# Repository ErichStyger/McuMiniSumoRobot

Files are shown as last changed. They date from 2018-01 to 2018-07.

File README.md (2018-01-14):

# McuMiniSumoRobot
This project implements the hardare and software for a Mini Sumo Robot.
The project has been started and created by Simon Herzog as part of the PAIND course at the Lucerne University of Applied Sciences and Arts in the Fall 2017 semester.

This small (10x10 cm) competitive, cost effective Mini Sumo robot is itended to be used for
- robotics courses
- computer science courses
- electrical engineering courses
- MINT and STEM activites
- show case for conferences and exhibitions 
- fun projects

See https://github.com/ErichStyger/McuMiniSumoRobot/wiki for more details about this project.

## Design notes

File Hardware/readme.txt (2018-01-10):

This folder contains the hardware/PCB files and information (KiCAD).
The V1 folder contains the first version of the PCB.

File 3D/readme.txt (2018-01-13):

This folder contains 3D models for 3D printing.
Autodesk 123D Design has been used to create the .123dx files.

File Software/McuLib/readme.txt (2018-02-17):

readme.txt
----------
This folder McuLib contains files from the McuOnEclipse library:
https://github.com/ErichStyger/McuOnEclipseLib

This folder contains all the library sources:
- config: application specific configuration files
- src: source files

Middleware:
- FreeRTOS: FreeRTOS realtime operating system, optimized and tuned for Segger SystemView and Percepio Trace
- TraceRecorder: Percipio Tracealyzer library for FreeRTOS (https://percepio.com/tz/)
- SEGGER_RTT: Segger Realtime Terminal Library (https://www.segger.com/products/debug-probes/j-link/technology/real-time-transfer/about-real-time-transfer/)
- SEGGER_SysView: Segger Systemview Library for tracing FreeRTOS (https://www.segger.com/products/development-tools/systemview/)

Components of the McuOnEclipse (in alphabetical order):
- McuArmTools: various ARM Cortex utilities
- McuCriticalSection: critical section handling
- McuDS18B20: Driver for the DS18B20 One-Wire temperature sensor library
- McuEvents: event handling using a bit array
- McuFontDisplay: Font rendering for graphical displays
- McuFXOS8700: Driver for the NXP FXOS8700 accelerometer/magnetometer
- McuGDisplay: Driver for graphical displays
- McuGenericI2C: Generic I2C driver using hardware I2C or software I2C
- McuGenericSWI2C: Software (bit banging) I2C driver
- McuGenericSWSPI: Software (bit banging) SPI driver
- McuGFont: Graphical font library driver. Several fonts are available in the 'fonts' subfolder
- McuHardfault: ARM Cortex-M hardfault handler
- McuI2CSpy: I2C sniffing utility
- McuLED: generic LED driver
- McuLib: Configuration of the McuOnEclipse Library
- McuOneWire: 1-Wire communication driver
- McuPercepio: Configuration and interface to the Percepio Trace library
- McuPidFloat: Generic PID control loop using floating point values
- McuPidInt: Generic PID control loop using integer values
- McuQuadCounter: Quadrature Counter library
- McuRingBuffer: Generic Ring Buffer implementation
- McuRTOS: wrapper for FreeRTOS
- McuRTT: wrapper for Segger RTT
- McuSharpMemoryDisplay: Driver for the Sharp Memory displays
- McuShell: Driver for a command line shell
- McuSystemView: Wrapper for the Segger SystemViewer
- McuTimeDate: Realtime clock implementation for software, hardware and external I2C RTC
- McuTimeout: generic driver for timeout handling
- McuTrigger: generic interrupt callback handling
- McuUSB: interface and wrapper to the FSL USB Stack 4.1.1
- McuUtility: various safe string manipulation and other utility functions
- McuWait: Realtime synchronization waiting routines
- McuXFormat: tiny formatting and printing, similar to sprintf

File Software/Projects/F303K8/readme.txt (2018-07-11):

readme.txt
----------

Project for the Sumo robot using the STM32F303 Nucleo-3 board.

Open:
- display more robot status on LCD
- line following
- UART
- option: haptic feedback with wheels
- Use UART for one extra line sensor and to turn off IR LEDs
- header for LCD, pull-ups

Custom configuration settings (McuLib/config):
- McuShellconfig.h
- McuSSD1306config.h
- McuGenericI2Cconfig.h

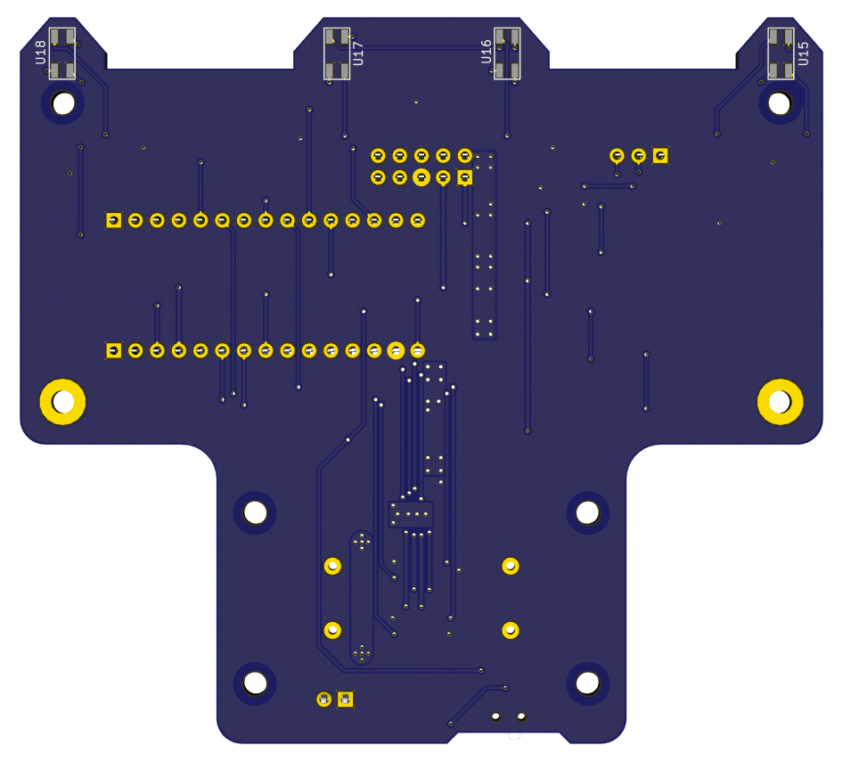
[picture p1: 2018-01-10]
Hardware/V1a/3D_PCB_bottom.png

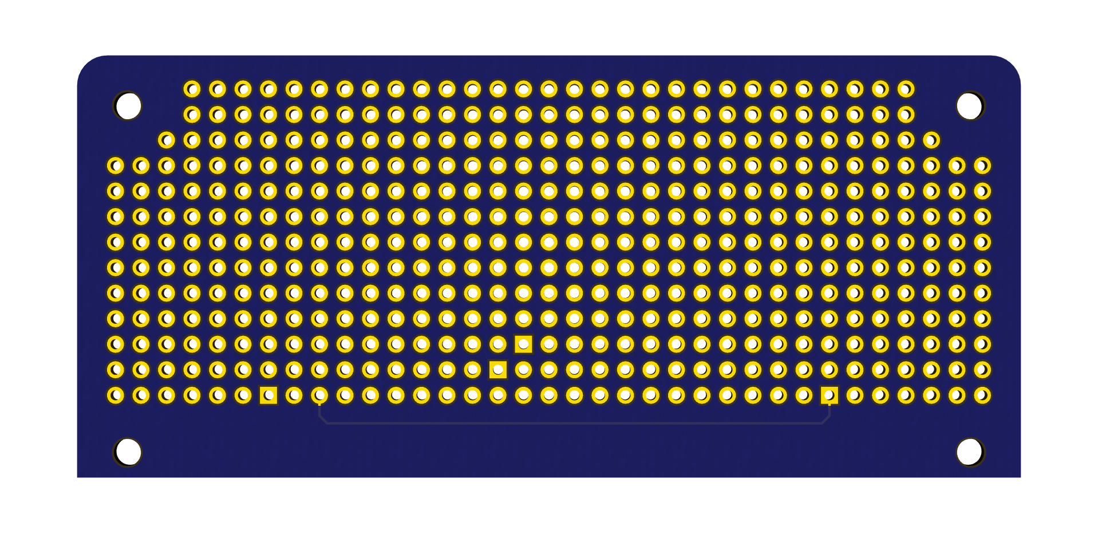
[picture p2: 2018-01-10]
Hardware/V1a/3D_PCB_top_back.png

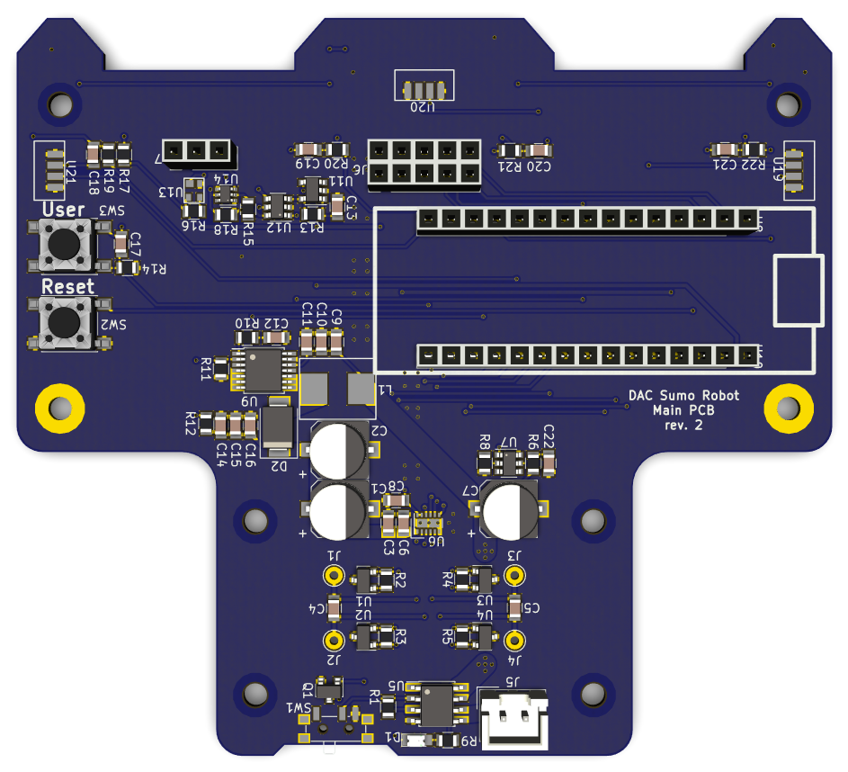
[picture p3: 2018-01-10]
Hardware/V1a/3D_PCB_top.png

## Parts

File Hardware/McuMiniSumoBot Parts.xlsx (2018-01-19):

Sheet: Summary
Cost estimate for a single Robot
 | Total | CHF 112.50 |  |  |  | CHF 96.40 | CHF 17.23
Vendor | Order Number | Shipping | Min | Add | Price | Total |  | Description | Comment | Link
Mouser | 710-15400394A3590 |  | 6 |  | 0.42 | 2.53 | 0.00 | Standard LEDs - Through Hole WL-TIRW THT Infrared Waterclr Rnd 5mm 940 nm |  | https://www.mouser.ch/productdetail/wurth-electronics/15400394a3590
Mouser | Various |  | 1 |  | 27.11 | 27.11 | 0.00 | PCB Parts, see other Tab | See other tab with details
Mouser | 511-NUCLEO-F303K8 |  | 1 |  | 10.50 | 10.50 | 0.00 | Nucleo |  | https://www.mouser.ch/ProductDetail/STMicroelectronics/NUCLEO-F303K8/
Banggood | 969144 |  | 0 | 1 | 6.18 | 0.00 | 6.18 | 0.96 Inch 4Pin Blue Yellow IIC I2C OLED Display Module For Arduino | Order pack of 3 | https://www.banggood.com/0_96-Inch-4Pin-Blue-Yellow-IIC-I2C-OLED-Display-Module-For-Arduino-p-969144.html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
Banggood | 969147 |  |  | 1 | 6.28 |  |  | 0.96 Inch 4Pin IIC I2C Blue OLED Display Module For Arduino |  | https://www.banggood.com/0_96-Inch-4Pin-IIC-I2C-Blue-OLED-Display-Module-For-Arduino-p-969147.html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
Banggood | 924048 |  | 1 |  | 1.53 | 1.53 | 0.00 | USB Lithium Battery Charger Module Board With Charging And Protection | Oder pack of 3 | https://www.banggood.com/USB-Lithium-Battery-Charger-Module-Board-With-Charging-And-Protection-p-924048.html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
Banggood | 1091243 |  | 1 | 4 | 2.76 | 2.76 | 11.05 | 5Pcs XF Power 3.7V 600mAh 1S 30C Fabric Cable LiPo Battery White Plug | Order pack of 5 | https://www.banggood.com/XF-Power-3_7V-600mAh-1S-30C-Fabric-Cable-LiPo-Battery-White-Plug-p-1091243.html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
Banggood | 1044078 |  | 1 |  | 2.52 | 2.52 | 0.00 | 10 Pairs 1S Battery Charging Cable Male & Female | Use correct connector instead
Banggood | Shipping |  |  |  |  | 0.00 | 0.00 |  | Usually free of charge shipping | https://www.pcbway.com/
PCBWay | Shipping | CHF 11.00 |  |  |  | 0.00 | 0.00
PCBWay | PCB |  | 1 |  | 5.00 | 5.00 | 0.00 | PCB 10x10 dual layer | 5-10 PCBs for a total of $5!
Jsumo | SLT20 |  | 1 |  | 16.00 | 16.00 | 0.00 | SLT20 Silicon Wheel Set
Jsumo | SLT20P |  |  |  | 18.00 | 0.00 | 0.00 | SLT20 Silicon Wheel Set with steel hub | Recommended
Jsumo | Shipping | CHF 40.00 |  |  |  | 0.00 | 0.00 |  | Free shipping from $199
Fingertech |  |  |  |  |  | 0.00 | 0.00 |  | Alternative wheels, don't forget Hex Wrench!
Pololu | 1127 |  |  |  | 3.56 | 0.00 | 0.00 | 1: Solarbotics RW2i Wheel (internal set screw) | Alternative wheels, don't forget Hex Wrench! | https://www.pololu.com/product/1127
Pololu | 2214 |  |  |  | 16.95 | 0.00 | 0.00 | 2: 100:1 Micro Metal Gearmotor HP 6V with Extended Motor Shaft | 1:75, 1:100 and 1:150 alternatives | https://www.pololu.com/product/2214
Pololu | 2599 |  | 1 |  | 3.45 | 3.45 | 0.00 | Magnetic Encoder Disc for Micro Metal Gearmotors, OD 7.65 mm, ID 1.0 mm, 12 CPR (Bulk) | Bulk 5 pieces
Pololu | Shipping | CHF 40.00 |  |  |  | 0.00 | 0.00
Mouser | Shipping | CHF 8.00 |  |  |  | 0.00 | 0.00 |  | Free shipping inside US
TinySine | Shipping | CHF 6.00 |  |  |  | 0.00 | 0.00
TinySine | G5A1518B927942 | CHF 7.50 | 2 |  | 7.50 | 15.00 | 0.00 | Micro Metal Gearmotor HP 6V with Extended Motor Shaft 1.6A - 100:1 |  | https://www.tinyosshop.com/index.php?route=product/product&path=64_82&product_id=1051
Misc | Misc small parts |  | 1 |  | 10.00 | 10.00 | 0.00

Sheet: PCB Parts
DAC SUMO ROBOT |  |  |  |  |  |  |  |  | 27.11
Mouser-Nr. | Herst.- Nr. | Hersteller | Kunden-Teilenr | Beschreibung | RoHS | Lebenszyklus | Stückzahl | Preis (CHF) | Gesamtpreis: (CHF)
80-EDH227M010A9HAA | EDH227M010A9HAA | KEMET |  | Alu-Elektrolytkondensatoren - SMD 10V 220uF 20% | RoHS-konform | Neues Produkt | 3 | 0.343 fr. | 1.03
511-STTH4R02U | STTH4R02U | STMicroelectronics |  | Gleichrichter RECTIFIER | RoHS-konform |  | 1 | 0.782 fr. | 0.78
771-NX7002AKVL | NX7002AKVL | Nexperia |  | MOSFET NX7002AK/TO-236AB/REEL 11" Q3/ | RoHS-konform |  | 1 | 0.117 fr. | 0.12
688-SSSS811101 | SSSS811101 | ALPS |  | Schiebeschalter SPDT HORZ GRND 1.5mm | RoHS-konform |  | 1 | 1.21 fr. | 1.21
926-LM2700MTXADJNOPB | LM2700MTX-ADJ/NOPB | Texas Instruments |  | Schaltspannungsregler 600kHz/1.25MHz, 2.5A, Step-up PWM DC/DC | RoHS-konform |  | 1 | 3.61 fr. | 3.61
595-DRV8835DSSR | DRV8835DSSR | Texas Instruments |  | Motor / Bewegung / Zündungscontroller und Treiber 1.5A Low Vlt Stepper Motor | RoHS-konform |  | 1 | 1.81 fr. | 1.81
78-TSSP77038TR | TSSP77038TR | Vishay |  | Infrarot-Receiver IR Receiver Module | RoHS-konform |  | 3 | 1.75 fr. | 5.25
595-DRV5013ADQDBZR | DRV5013ADQDBZR | Texas Instruments |  | Halleffekt-/Magnetsensoren für Plattenmontage 2.5-38V Dig Latch Hall Sensor | RoHS-konform |  | 4 | 0.831 fr. | 3.32
595-SN74LVC1G18DBVR | SN74LVC1G18DBVR | Texas Instruments |  | Encoder, Decoder, Multiplexer u. Demultiplexer 1 of 2 Noninverting DeMultxr | RoHS-konform |  | 1 | 0.362 fr. | 0.36
998-MIC1557YM5TR | MIC1557YM5-TR | Microchip |  | Zeitgeber & Support-Produkte | RoHS-konform |  | 1 | 0.929 fr. | 0.93
512-QRE1113GR | QRE1113GR | ON Semiconductor |  | Optische Schalter, reflektierend, mit Fototransistor-Ausgang Reflective Sensor | RoHS-konform |  | 4 | 0.841 fr. | 3.36
757-SSM6N7002KFULF | SSM6N7002KFU,LF | Toshiba |  | MOSFET Small-signal MOSFET 2in1 ESD Protected | RoHS-konform | Neues Produkt | 1 | 0.254 fr. | 0.25
653-B3FS-1010 | B3FS-1010 | Omron |  | Sensorschalter 6x6x4.3mm 100gf | RoHS-konform |  | 2 | 0.684 fr. | 1.37
512-FDS4935BZ | FDS4935BZ | ON Semiconductor |  | MOSFET 30V PCH DUAL POWER TRENCH M | RoHS-konform |  | 1 | 0.91 fr. | 0.91
621-AP9101CAK6ABTRG1 | AP9101CAK6-ABTRG1 | Diodes Incorporated |  | Batterie-Management Protection IC 1-Cell LI 3.0uA 3.5V | RoHS-konform |  | 1 | 0.43 fr. | 0.43
963-LMK212BBJ226MG-T | LMK212BBJ226MG-T | Taiyo Yuden |  | Kondensator aus mehreren Keramikschichten MLCC - SMD/SMT 22uF 10V X5R +/-20% 0805 Gen Purp | RoHS-konform |  | 2 | 0.311 fr. | 0.62
726-BCR205WH6327 | BCR 205W H6327 | Infineon |  | LED-Beleuchtungstreiber Ultra lowdropout LED controllr up to 80mA | RoHS-konform |  | 1 | 0.44 fr. | 0.44
710-150080VS75000 | 150080VS75000 | Wurth Electronics |  | Standard-LEDs - SMD WL-SMCW SMDMono TpVw Waterclr 0805 BrtGrn | RoHS-konform |  | 1 | 0.184 fr. | 0.18
652-SRP7028A-4R7M | SRP7028A-4R7M | Bourns |  | Festinduktoren 4.7uH 20% SMD 7028 AEC-Q200 | RoHS-konform |  | 1 | 1.13 fr. | 1.13

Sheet: NOT included
0805 R and C
Shipping (might vary)
Battery connector
Screws
Standoffs
3D Prints
PCB Assembly
Robot assembly
Headers (optional)

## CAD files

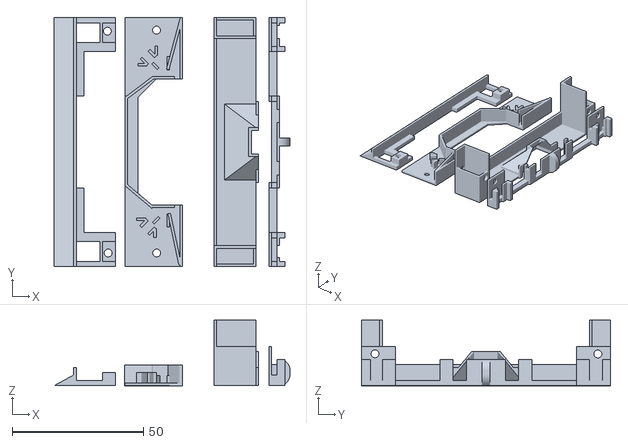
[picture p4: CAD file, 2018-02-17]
3D/FrontBlade.stl
90.0 x 95.1 x 25.1

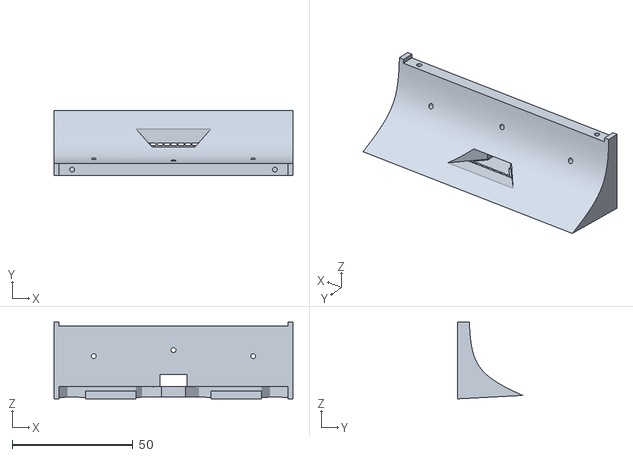
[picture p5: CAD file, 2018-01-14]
3D/Blade - Blade.stl
99.0 x 27.0 x 31.8

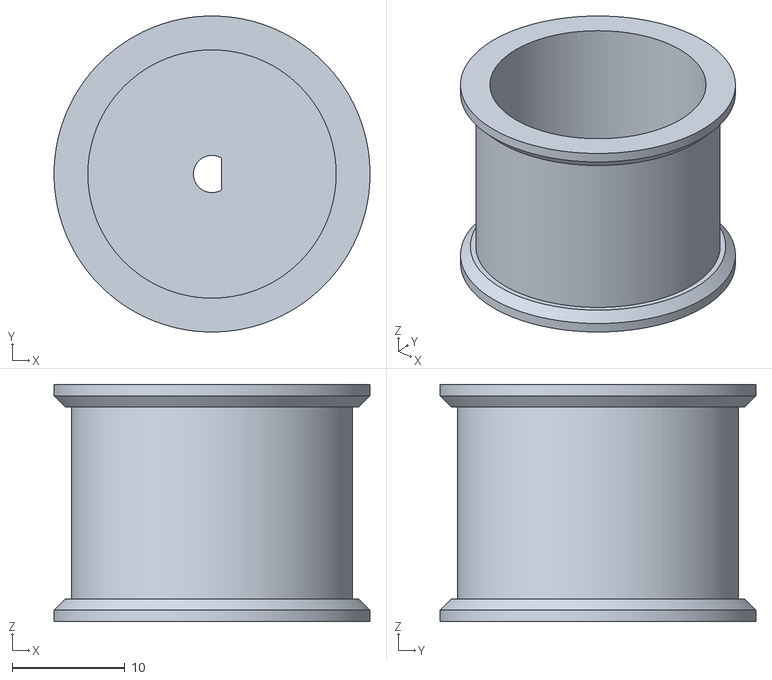
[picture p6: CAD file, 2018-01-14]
3D/Hub JSumo.stl
28.0 x 28.0 x 21.0

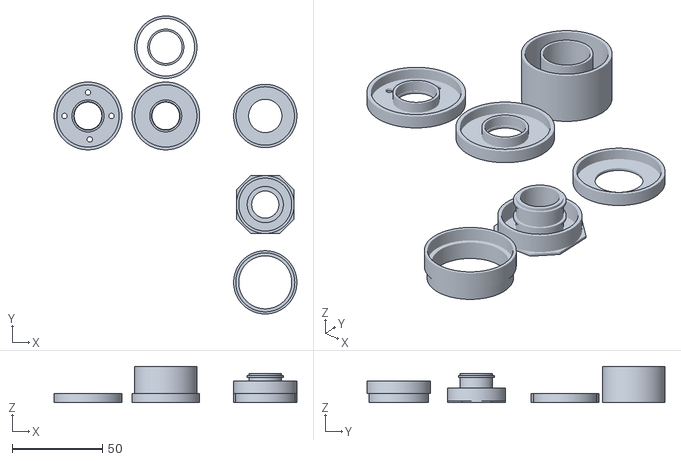
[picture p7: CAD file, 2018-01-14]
3D/TireMold.stl
134.2 x 164.7 x 20.0

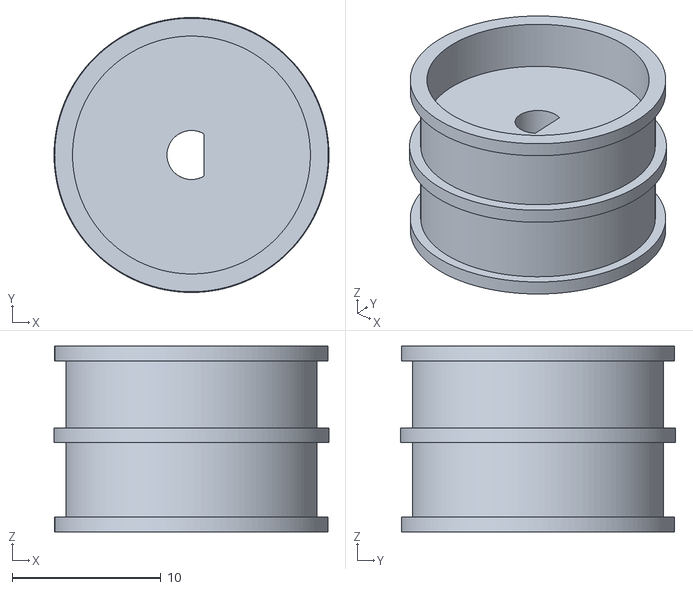
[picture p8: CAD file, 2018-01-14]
3D/Hub Solarbotics.stl
18.5 x 18.5 x 12.5

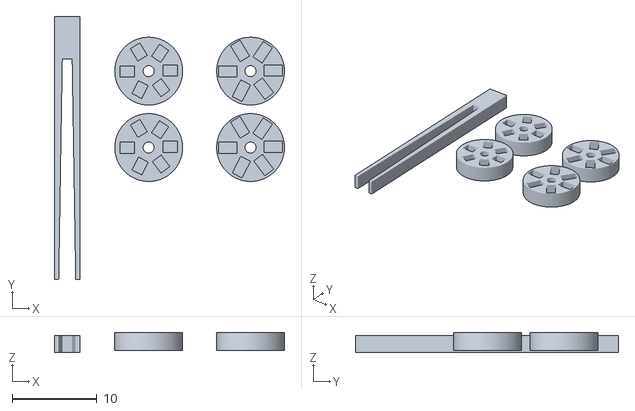
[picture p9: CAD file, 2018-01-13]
3D/MagneticDiskEncoder.stl
27.1 x 31.0 x 2.40

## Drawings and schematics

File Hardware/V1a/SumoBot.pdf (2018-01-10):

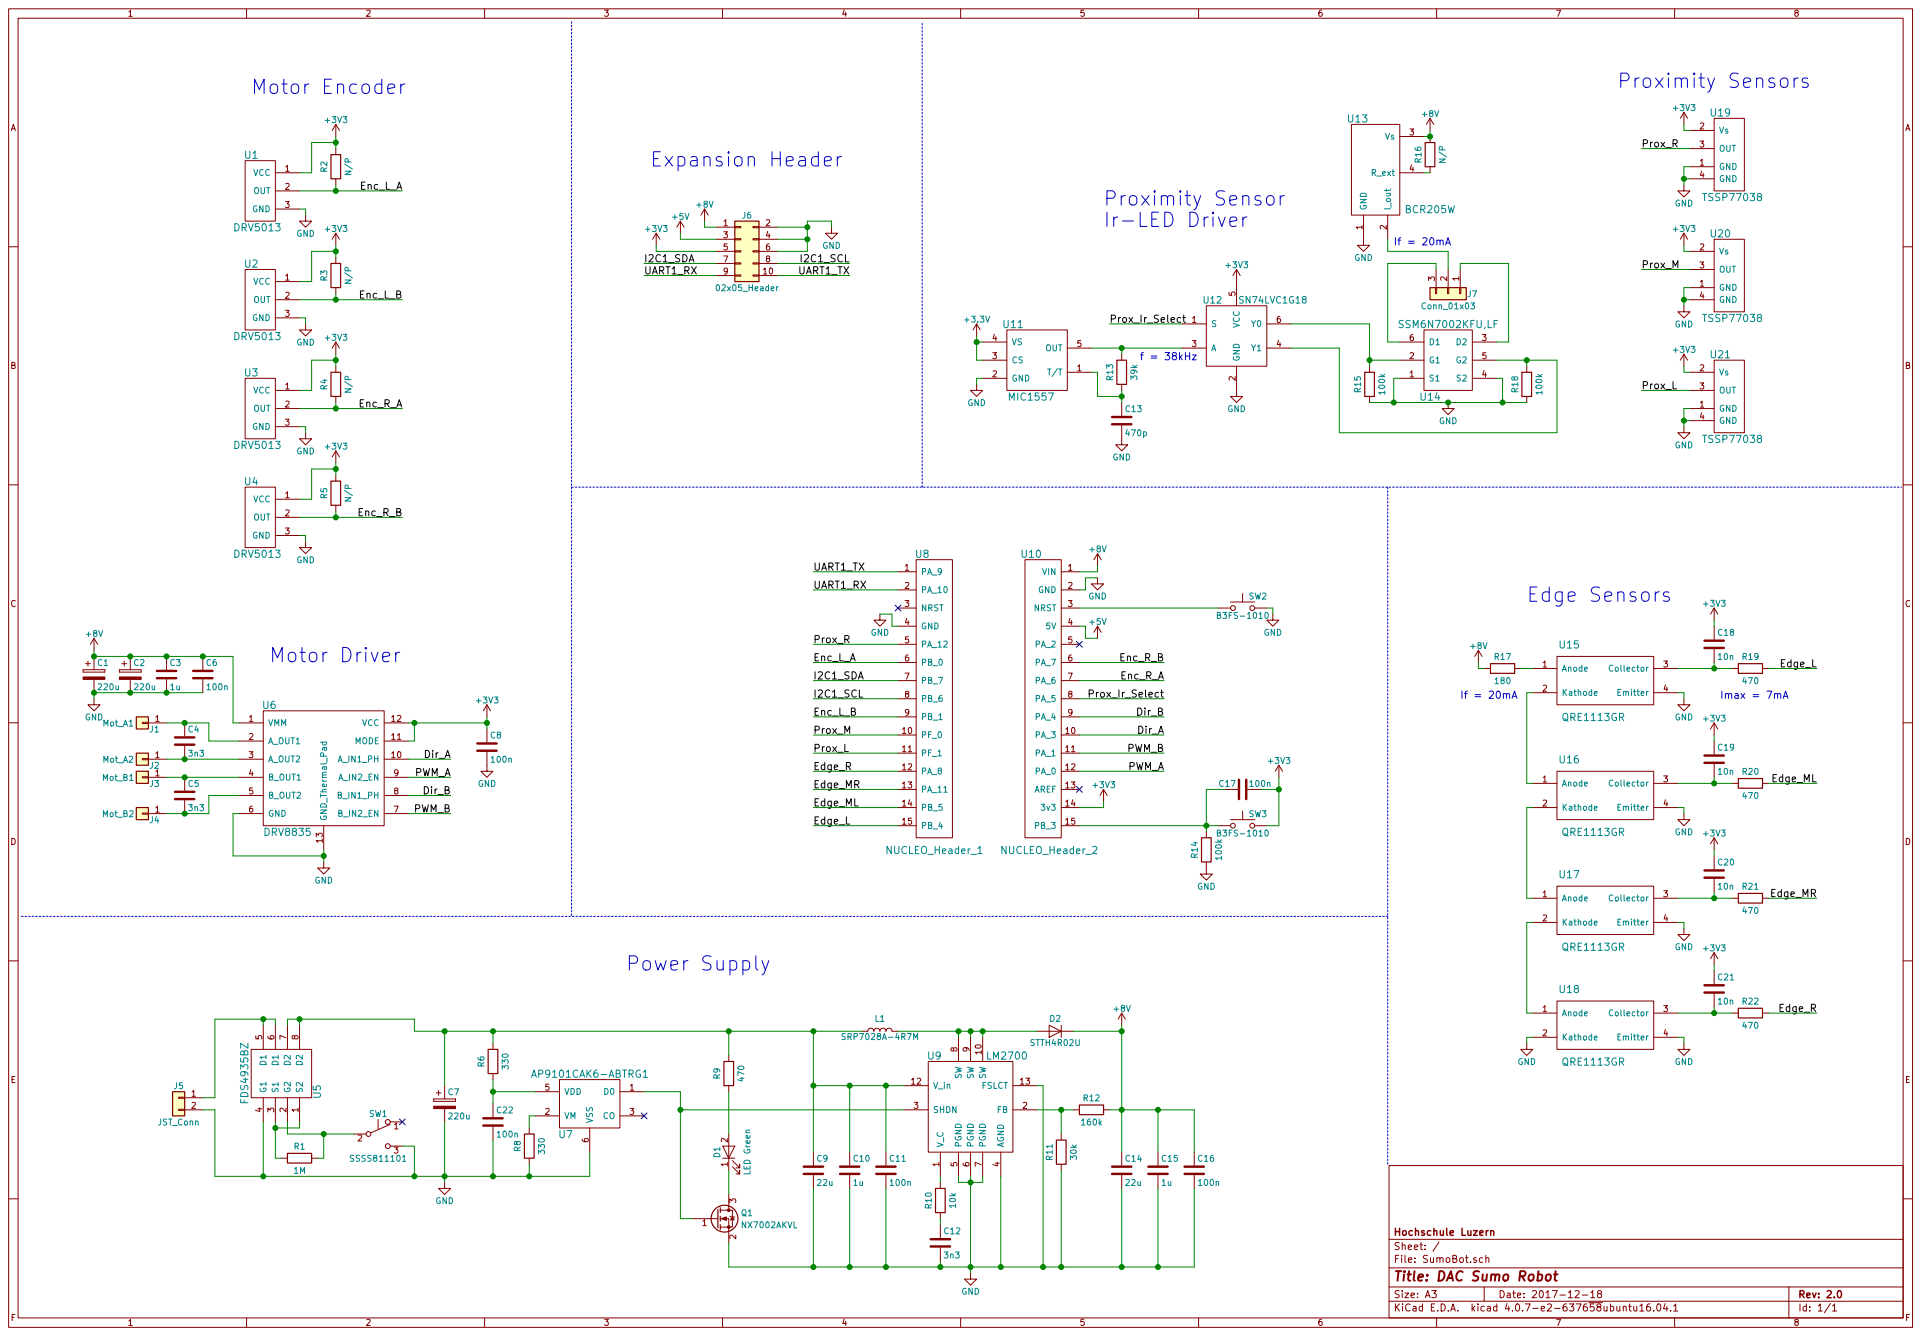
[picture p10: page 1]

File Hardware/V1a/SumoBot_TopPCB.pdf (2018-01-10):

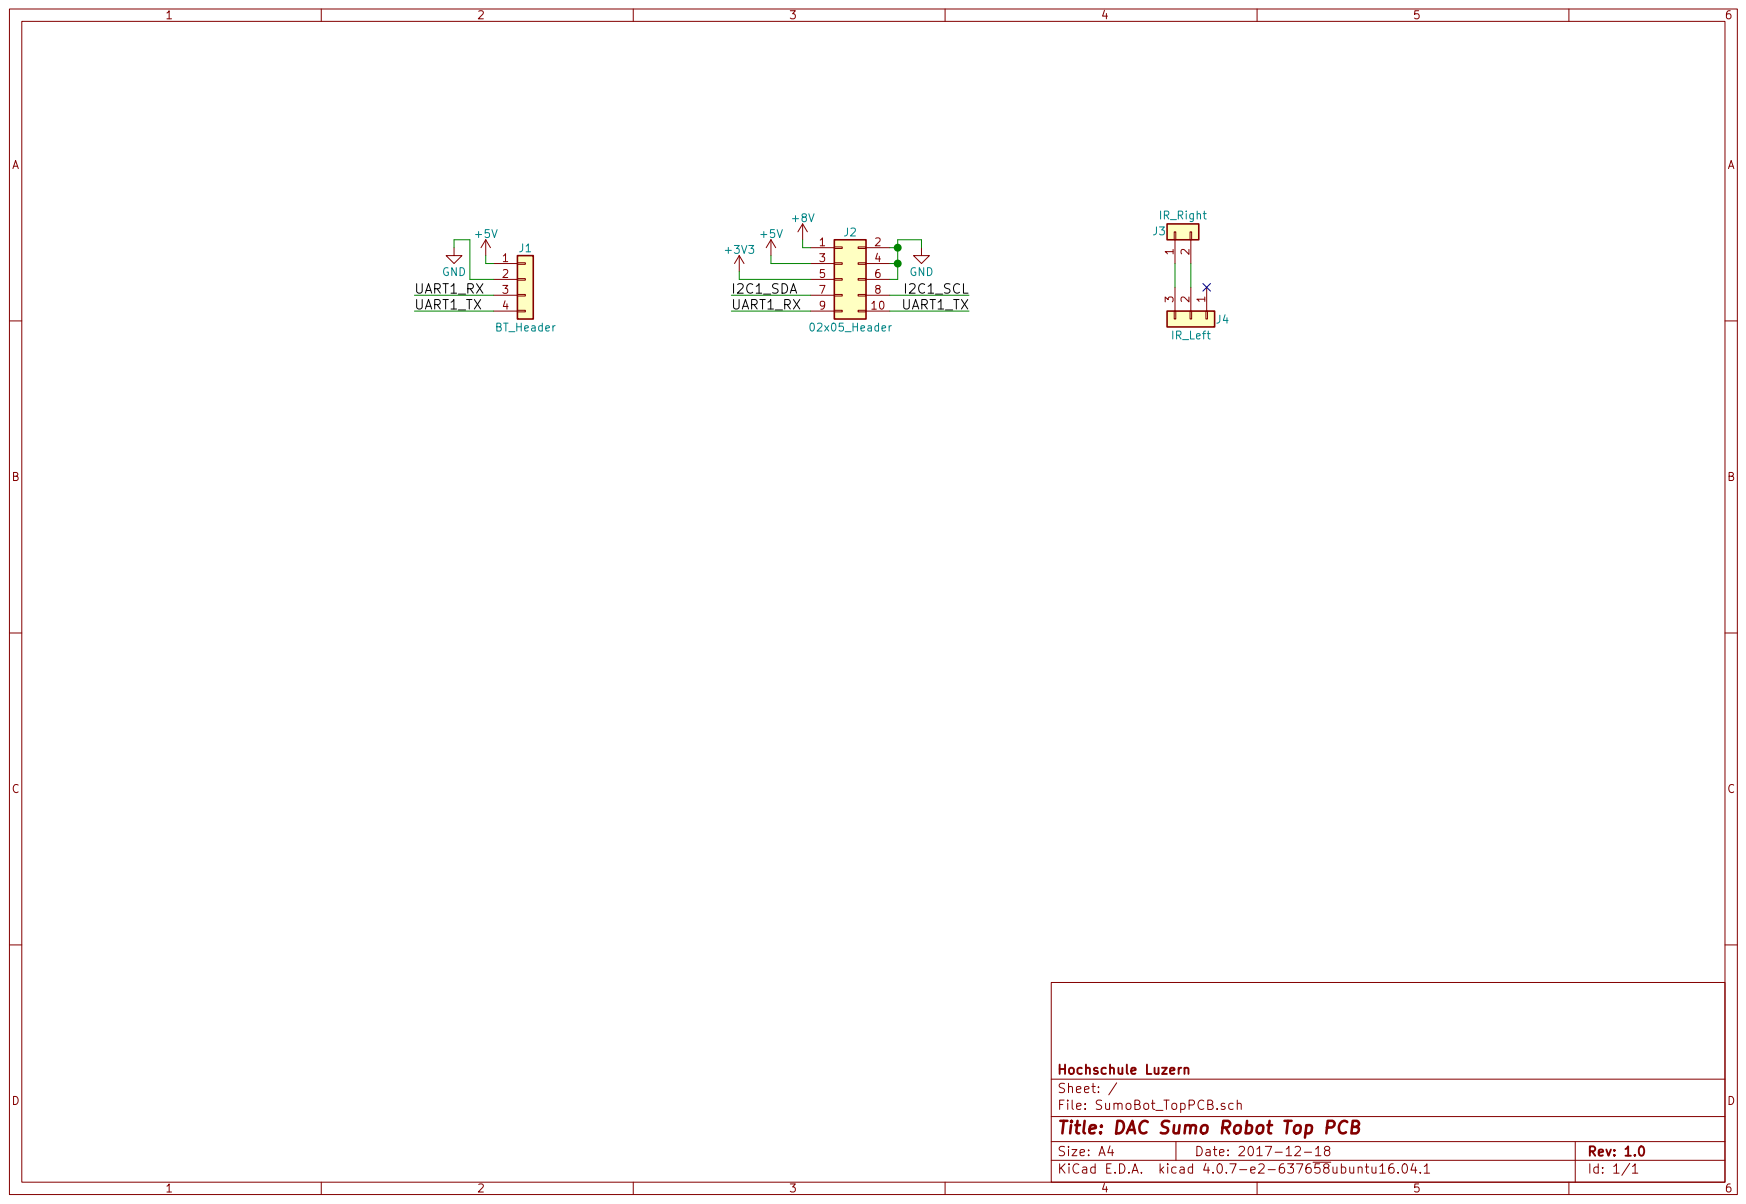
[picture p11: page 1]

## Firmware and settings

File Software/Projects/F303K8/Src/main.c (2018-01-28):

/**
 * \file
 * \brief Main entry point of the application.
 * \author Erich Styger, erich.styger@hslu.ch
 *
 * This module implements main() and configures the hardware.
 */

#include "Platform.h"
#include "main.h"
#include "Application.h"

/*!
 * \brief main application entry point
 * \return error code, 0 for no error
 */
int main(void) {
  /* PL_Init(); */ /* already called during startup! initialization of platform, board and drivers */
  APP_Run();
  for(;;) {
	  /* should not get here! */
  }
  return 0; /* main() never should return! */
}

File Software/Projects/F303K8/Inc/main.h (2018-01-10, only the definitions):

#define Prox_M_Pin GPIO_PIN_0
#define Prox_M_GPIO_Port GPIOF
#define Prox_L_Pin GPIO_PIN_1
#define Prox_L_GPIO_Port GPIOF
#define PWM_L_Pin GPIO_PIN_0
#define PWM_L_GPIO_Port GPIOA
#define PWM_R_Pin GPIO_PIN_1
#define PWM_R_GPIO_Port GPIOA
#define VCP_TX_Pin GPIO_PIN_2
#define VCP_TX_GPIO_Port GPIOA
#define Dir_A_Pin GPIO_PIN_3
#define Dir_A_GPIO_Port GPIOA
#define Dir_B_Pin GPIO_PIN_4
#define Dir_B_GPIO_Port GPIOA
#define Prox_Ir_Select_Pin GPIO_PIN_5
#define Prox_Ir_Select_GPIO_Port GPIOA
#define Enc_R_A_Pin GPIO_PIN_6
#define Enc_R_A_GPIO_Port GPIOA
#define Enc_R_B_Pin GPIO_PIN_7
#define Enc_R_B_GPIO_Port GPIOA
#define Enc_L_A_Pin GPIO_PIN_0
#define Enc_L_A_GPIO_Port GPIOB
#define Enc_L_B_Pin GPIO_PIN_1
#define Enc_L_B_GPIO_Port GPIOB
#define Edge_R_Pin GPIO_PIN_8
#define Edge_R_GPIO_Port GPIOA
#define Edge_MR_Pin GPIO_PIN_11
#define Edge_MR_GPIO_Port GPIOA
#define Prox_R_Pin GPIO_PIN_12
#define Prox_R_GPIO_Port GPIOA
#define SWDIO_Pin GPIO_PIN_13
#define SWDIO_GPIO_Port GPIOA
#define SWCLK_Pin GPIO_PIN_14
#define SWCLK_GPIO_Port GPIOA
#define VCP_RX_Pin GPIO_PIN_15
#define VCP_RX_GPIO_Port GPIOA
#define Usr_But_Pin GPIO_PIN_3
#define Usr_But_GPIO_Port GPIOB
#define Edge_L_Pin GPIO_PIN_4
#define Edge_L_GPIO_Port GPIOB
#define Edge_ML_Pin GPIO_PIN_5
#define Edge_ML_GPIO_Port GPIOB

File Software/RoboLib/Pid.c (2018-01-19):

/**
 * \file
 * \brief This is the implementation of the PID Module
 * \author Erich Styger, erich.styger@hslu.ch
 */

#include "Platform.h"
#if PL_CONFIG_HAS_PID
#include "Pid.h"
#include "Motor.h"
#include "McuUtility.h"
#include "Reflectance.h"

#define PID_DEBUG 0 /* careful: this will slow down the PID loop frequency! */

#if PL_CONFIG_HAS_LINE_PID
  static PID_Config lineFwConfig;
#endif
#if PL_CONFIG_GO_DEADEND_BW
  static PID_Config lineBwConfig;
#endif
#if PL_CONFIG_HAS_POS_PID
  static PID_Config posLeftConfig, posRightConfig;
#endif
#if PL_CONFIG_HAS_SPEED_PID
  static PID_Config speedLeftConfig, speedRightConfig;
#endif
  
uint8_t PID_GetPIDConfig(PID_ConfigType config, PID_Config **confP) {
  switch(config) {
#if PL_CONFIG_HAS_LINE_PID
    case PID_CONFIG_LINE_FW:
      *confP = &lineFwConfig; break;
#endif
#if PL_CONFIG_GO_DEADEND_BW
    case PID_CONFIG_LINE_BW:
      *confP = &lineBwConfig; break;
#endif
    case PID_CONFIG_POS_LEFT:
      *confP = &posLeftConfig; break;
    case PID_CONFIG_POS_RIGHT:
      *confP = &posRightConfig; break;
    case PID_CONFIG_SPEED_LEFT:
      *confP = &speedLeftConfig; break;
    case PID_CONFIG_SPEED_RIGHT:
      *confP = &speedRightConfig; break;
    default:
      *confP = NULL;
      return ERR_FAILED;
  }
  return ERR_OK;
}

#if PL_CONFIG_HAS_SPEED_PID || PL_CONFIG_HAS_POS_PID || PL_CONFIG_HAS_LINE_PID
static int32_t PID(int32_t currVal, int32_t setVal, PID_Config *config) {
  int32_t error;
  int32_t pid;
  
  /* perform PID closed control loop calculation */
  error = setVal-currVal; /* calculate error */
  pid = (error*config->pFactor100)/100; /* P part */
  config->integral += error; /* integrate error */
  if (config->integral>config->iAntiWindup) {
    config->integral = config->iAntiWindup;
  } else if (config->integral<-config->iAntiWindup) {
    config->integral = -config->iAntiWindup;
  }
#if 1 /* see http://brettbeauregard.com/blog/2011/04/improving-the-beginner%E2%80%99s-pid-reset-windup/ */
  {
    int32_t max;

    max = 0xffff; /* max value of PWM */
    if (config->integral > max) {
      config->integral = max;
    } else if (config->integral < -max) {
      config->integral = -max;
    }
  }
#endif
  pid += (config->integral*config->iFactor100)/100; /* add I part */
  pid += ((error-config->lastError)*config->dFactor100)/100; /* add D part */
  config->lastError = error; /* remember for next iteration of D part */
  return pid;
}
#endif

#if PL_CONFIG_HAS_LINE_PID
static int32_t Limit(int32_t val, int32_t minVal, int32_t maxVal) {
  if (val<minVal) {
    return minVal;
  } else if (val>maxVal) {
    return maxVal;
  }
  return val;
}

#if 0
static MOT_Direction AbsSpeed(int32_t *speedP) {
  if (*speedP<0) {
    *speedP = -(*speedP);
    return MOT_DIR_BACKWARD;
  }
  return MOT_DIR_FORWARD;
}
#endif

#if 0
/*! \brief returns error (always positive) percent */
static uint8_t errorWithinPercent(int32_t error) {
  if (error<0) {
    error = -error;
  }
  error = error/(REF_MAX_LINE_VALUE/2/100);
  if (error>100) {
    error = 100;
  }
  return error;
}
#endif

#if PL_APP_LINE_FOLLOWING || PL_APP_LINE_MAZE
static void PID_LineCfg(uint16_t currLine, uint16_t setLine, uint16_t currLineWidth, bool forward, PID_Config *config) {
  int32_t pid, speed, speedL, speedR;
#if PID_DEBUG
  unsigned char buf[16];
  static uint8_t cnt = 0;
#endif
//  uint8_t errorPercent;
  MOT_Direction directionL=MOT_DIR_FORWARD, directionR=MOT_DIR_FORWARD;
  
  (void)currLineWidth;

  pid = PID(currLine, setLine, config);
  //errorPercent = errorWithinPercent(currLine-setLine);
  
  /* transform into different speed for motors. The PID is used as difference value to the motor PWM */
  if (!forward) { /* going backward */
    /* need to do it slow as sensor is on the 'back', and we cannot usual turns to get the sensor back 'on line' */
    speed = ((int32_t)config->maxSpeedPercent)*(0xffff/100)*6/10; /* %60 */
    pid = Limit(pid, -speed, speed);
    if (pid<0) { /* turn right */
      speedR = speed;
      speedL = speed-pid;
    } else { /* turn left */
      speedR = speed+pid;
      speedL = speed;
    }
#if 0 /* simple differential steering */
  } else {
    speed = ((int32_t)config->maxSpeedPercent)*(0xffff/100); /* 100% */
    pid = Limit(pid, -speed, speed);
    if (pid<0) { /* turn right */
      speedR = speed;
      speedL = speed-pid;
    } else { /* turn left */
      speedR = speed+pid;
      speedL = speed;
    }
  }
#elif 1 || PL_DO_MINT /* aggressive line following! */
  } else {
    speed = ((int32_t)config->maxSpeedPercent)*(0xffff/100); /* scale to base speed */
    if (pid<0) { /* turn right */
      speedR = speed+pid; /* decrease speed */
      speedL = speed-pid; /* increase speed */
    } else { /* turn left */
      speedR = speed+pid; /* increase speed */
      speedL = speed-pid; /* decrease speed */
    }
  }
#else
  } else if (errorPercent <= 20) { /* pretty on center: move forward both motors with base speed */
    speed = ((int32_t)config->maxSpeedPercent)*(0xffff/100); /* 100% */
    pid = Limit(pid, -speed, speed);
    if (pid<0) { /* turn right */
      speedR = speed;
      speedL = speed-pid;
    } else { /* turn left */
      speedR = speed+pid;
      speedL = speed;
    }
  } else if (errorPercent <= 30) {
    /* outside left/right halve position from center, slow down one motor and speed up the other */
//    speed = ((int32_t)config->maxSpeedPercent)*(0xffff/100)*10/10; /* 80% */
    speed = 50*(0xffff/100);
    pid = Limit(pid, -speed, speed);
    if (pid<0) { /* turn right */
      speedR = speed+pid; /* decrease speed */
      speedL = speed-pid; /* increase speed */
    } else { /* turn left */
      speedR = speed+pid; /* increase speed */
      speedL = speed-pid; /* decrease speed */
    }
  } else if (errorPercent <= 60) {
//    speed = ((int32_t)config->maxSpeedPercent)*(0xffff/100)*10/10; /* %70 */
    speed = 80*(0xffff/100);
    pid = Limit(pid, -speed, speed);
    if (pid<0) { /* turn right */
      speedR = 0 /*maxSpeed+pid*/; /* decrease speed */
      speedL = speed-pid; /* increase speed */
    } else { /* turn left */
      speedR = speed+pid; /* increase speed */
      speedL = 0 /*maxSpeed-pid*/; /* decrease speed */
    }
  } else  {
    /* line is far to the left or right: use backward motor motion */
//    speed = ((int32_t)config->maxSpeedPercent)*(0xffff/100)*10/10; /* %100 */
    speed = 100*(0xffff/100);
    if (pid<0) { /* turn right */
      speedR = -speed+pid; /* decrease speed */
      speedL = speed-pid; /* increase speed */
    } else { /* turn left */
      speedR = speed+pid; /* increase speed */
      speedL = -speed-pid; /* decrease speed */
    }
    speedL = Limit(speedL, -speed, speed);
    speedR = Limit(speedR, -speed, speed);
    directionL = AbsSpeed(&speedL);
    directionR = AbsSpeed(&speedR);
  }
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

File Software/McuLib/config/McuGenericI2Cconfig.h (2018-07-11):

/**
 * \file
 * \brief Configuration header file for GenericI2C
 *
 * This header file is used to configure settings of the Generic I2C module.
 */

#ifndef __McuGenericI2C_CONFIG_H
#define __McuGenericI2C_CONFIG_H

#if !defined(McuGenericI2C_CONFIG_USE_ON_REQUEST_BUS_EVENT)
  #define McuGenericI2C_CONFIG_USE_ON_REQUEST_BUS_EVENT    (1)
    /*!< 1: generate user events for requesting bus; 0: no user events */
  #define McuGenericI2C_CONFIG_ON_REQUEST_BUS_EVENT   McuGenericI2C_OnRequestBus
  void McuGenericI2C_CONFIG_ON_REQUEST_BUS_EVENT(void); /* prototype */
#endif

#if !defined(McuGenericI2C_CONFIG_USE_ON_RELEASE_BUS_EVENT)
  #define McuGenericI2C_CONFIG_USE_ON_RELEASE_BUS_EVENT    (1)
    /*!< 1: generate user events for releasing bus; 0: no user events */
  #define McuGenericI2C_CONFIG_ON_RELEASE_BUS_EVENT   McuGenericI2C_OnReleaseBus
  void McuGenericI2C_CONFIG_ON_RELEASE_BUS_EVENT(void); /* prototype */
#endif

#if !defined(McuGenericI2C_CONFIG_USE_ON_ERROR_EVENT)
  #define McuGenericI2C_CONFIG_USE_ON_ERROR_EVENT    (1)
    /*!< 1: generate user events for errors; 0: no error events */
  #define McuGenericI2C_CONFIG_ON_ERROR_EVENT   McuGenericI2C_OnError
  void McuGenericI2C_CONFIG_ON_ERROR_EVENT(void); /* prototype */
#endif

#if !defined(McuGenericI2C_CONFIG_USE_MUTEX)
  #define McuGenericI2C_CONFIG_USE_MUTEX             (1)
    /*!< 1: Use a mutex to protect access to the bus; 0: no mutex used */
#endif

#if !defined(McuGenericI2C_CONFIG_WRITE_BUFFER_SIZE)
  #define McuGenericI2C_CONFIG_WRITE_BUFFER_SIZE             (32)
    /*!< Size of the write buffer size which defines the maximum block size which can be sent */
#endif

#if !defined(McuGenericI2C_CONFIG_SUPPORT_STOP_NO_START)
  #define McuGenericI2C_CONFIG_SUPPORT_STOP_NO_START      (0)
    /*!< 1: send a STOP condition without sending a new START condition. Currently only supported for the GenericSWI2C component. 0: send a STOP for every START */
#endif

/* configuration of function names used for low level I2C functions */
#include "McuGenericSWI2C.h" /* interface of low level I2C driver */

#include "Platform.h"
#if PL_CONFIG_HAS_SW_I2C

#define McuGenericI2C_CONFIG_RECV_BLOCK                        McuGenericSWI2C_RecvBlock
#define McuGenericI2C_CONFIG_SEND_BLOCK                        McuGenericSWI2C_SendBlock
#if McuGenericI2C_CONFIG_SUPPORT_STOP_NO_START
#define McuGenericI2C_CONFIG_SEND_BLOCK_CONTINUE               McuGenericSWI2C_SendBlockContinue
#endif
#define McuGenericI2C_CONFIG_SEND_STOP                         McuGenericSWI2C_SendStop
#define McuGenericI2C_CONFIG_SELECT_SLAVE                      McuGenericSWI2C_SelectSlave
#define McuGenericI2C_CONFIG_RECV_BLOCK_CUSTOM                 McuGenericSWI2C_RecvBlockCustom
#define McuGenericI2C_CONFIG_RECV_BLOCK_CUSTOM_AVAILABLE       (defined(McuGenericSWI2C_RECVBLOCKCUSTOM_AVAILABLE) && (McuGenericSWI2C_RECVBLOCKCUSTOM_AVAILABLE==1))
#else
#include "McuSTM32HALI2C.h" /* interface of low level I2C driver */
#define McuGenericI2C_CONFIG_RECV_BLOCK                        McuSTM32HALI2C_RecvBlock
#define McuGenericI2C_CONFIG_SEND_BLOCK                        McuSTM32HALI2C_SendBlock
#define McuGenericI2C_CONFIG_SEND_STOP                         McuSTM32HALI2C_SendStop
#define McuGenericI2C_CONFIG_SELECT_SLAVE                      McuSTM32HALI2C_SelectSlave
#define McuGenericI2C_CONFIG_RECV_BLOCK_CUSTOM                 McuSTM32HALI2C_RecvBlockCustom
#define McuGenericI2C_CONFIG_RECV_BLOCK_CUSTOM_AVAILABLE       (defined(McuSTM32HALI2C_RECVBLOCKCUSTOM_AVAILABLE) && (McuSTM32HALI2C_RECVBLOCKCUSTOM_AVAILABLE==1))
#endif

#endif /* __McuGenericI2C_CONFIG_H */

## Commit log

2018-01-10 added KiCad files
    [BOM_Sumo.xls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]
2018-01-10 added encoder with wheel and exetended sumo support
2018-01-12 various extensions and smaller bug fixes
    [LCD.c, Quadrature.c]
2018-01-13 added 3D models
    [MagneticDiskEncoder.stl]
2018-01-14 added model for 2 serial magnets in in disk
2018-01-14 added more 3D models
    [Blade - Blade.stl, Hub JSumo.stl, Hub Solarbotics.stl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]
2018-01-16 added extra screens for calibration
2018-01-19 Updated PID handling, added laser cut file
    [FrontBlade.stl, McuMiniSumoBot Parts.xlsx]
2018-01-28 updated 3D and laser cut files
    [FrontBlade.stl]
2018-02-17 updated 3D and manufacturing files
    [FrontBlade.stl]

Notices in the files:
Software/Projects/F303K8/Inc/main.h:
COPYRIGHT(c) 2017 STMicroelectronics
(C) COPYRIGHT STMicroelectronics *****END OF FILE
